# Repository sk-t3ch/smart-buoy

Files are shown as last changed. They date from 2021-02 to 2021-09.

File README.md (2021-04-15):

# [T3chFlicks](https://t3chflicks.org): Smart Buoy



> A complete ocean characteristic measuring and analytics system.
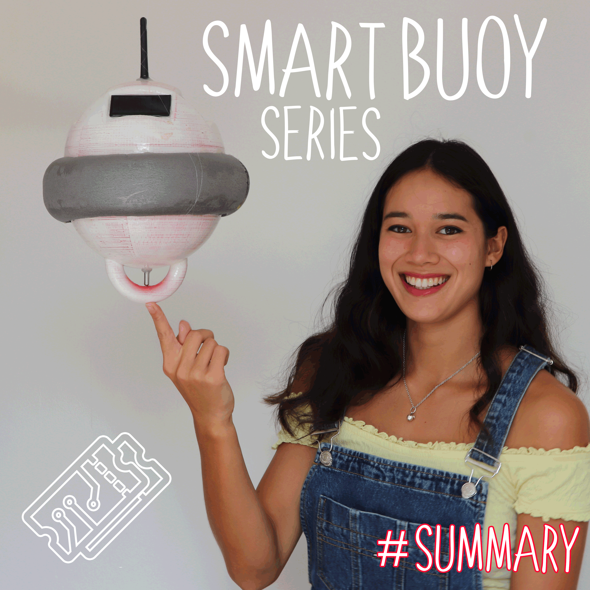
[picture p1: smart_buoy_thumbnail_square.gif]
gif_of_buoy


🎖️ Featured by [Raspberry Pi Blogs](https://www.raspberrypi.org/blog/good-buoy-the-raspberry-pi-smart-buoy/)

🎖️ Featured by [Hackaday](https://hackaday.com/2019/09/11/smart-buoy-rides-the-citizen-science-wave/)

🎖️ Featured by [Adafruit Blogs](https://blog.adafruit.com/2019/07/19/this-smart-buoy-measures-wave-height-period-power-and-more-piday-raspberrypi-raspberry_pi/)

🎖️ Featured by [Arduino](https://www.facebook.com/official.arduino/posts/3480468415312786)

🎖️ Featured by [Instructables](https://www.instructables.com/Smart-Buoy/)

🎖️ Second place [Instructables Sensor Contest](https://www.instructables.com/contest/sensors2019/)

---

## `tutorials/`
### Summary






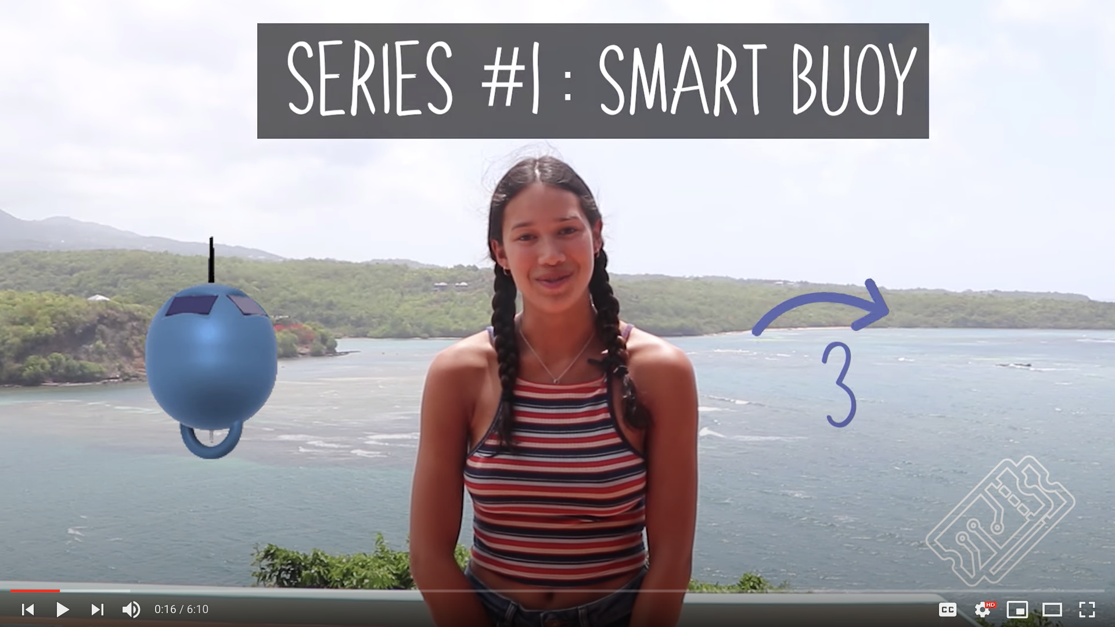
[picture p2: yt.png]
Everything Is AWESOME (https://www.youtube.com/watch?v=aLX4btGs_x8 "Youtube Video")
 

### 1. Wave and Temperature Measurements






### 2. GPS, Radio, and SD card






### 3. Scheduling Power






### 4. Waterproofing, Dashboards and Deploy






---

## `src/` - contains the source code for the whole project
* `buoy/` contains the code which runs on an Arduino inside the Buoy, as well as the build files (3d model, schematic etc).

* `baseStation/` contains the code for the server, database, and dashboard.
for the dashboard which is a VueJS application

---

## 💡 Product Showcase
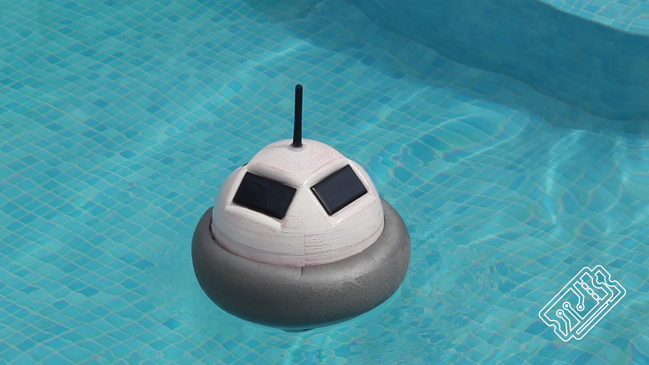
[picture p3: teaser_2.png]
Product
> 
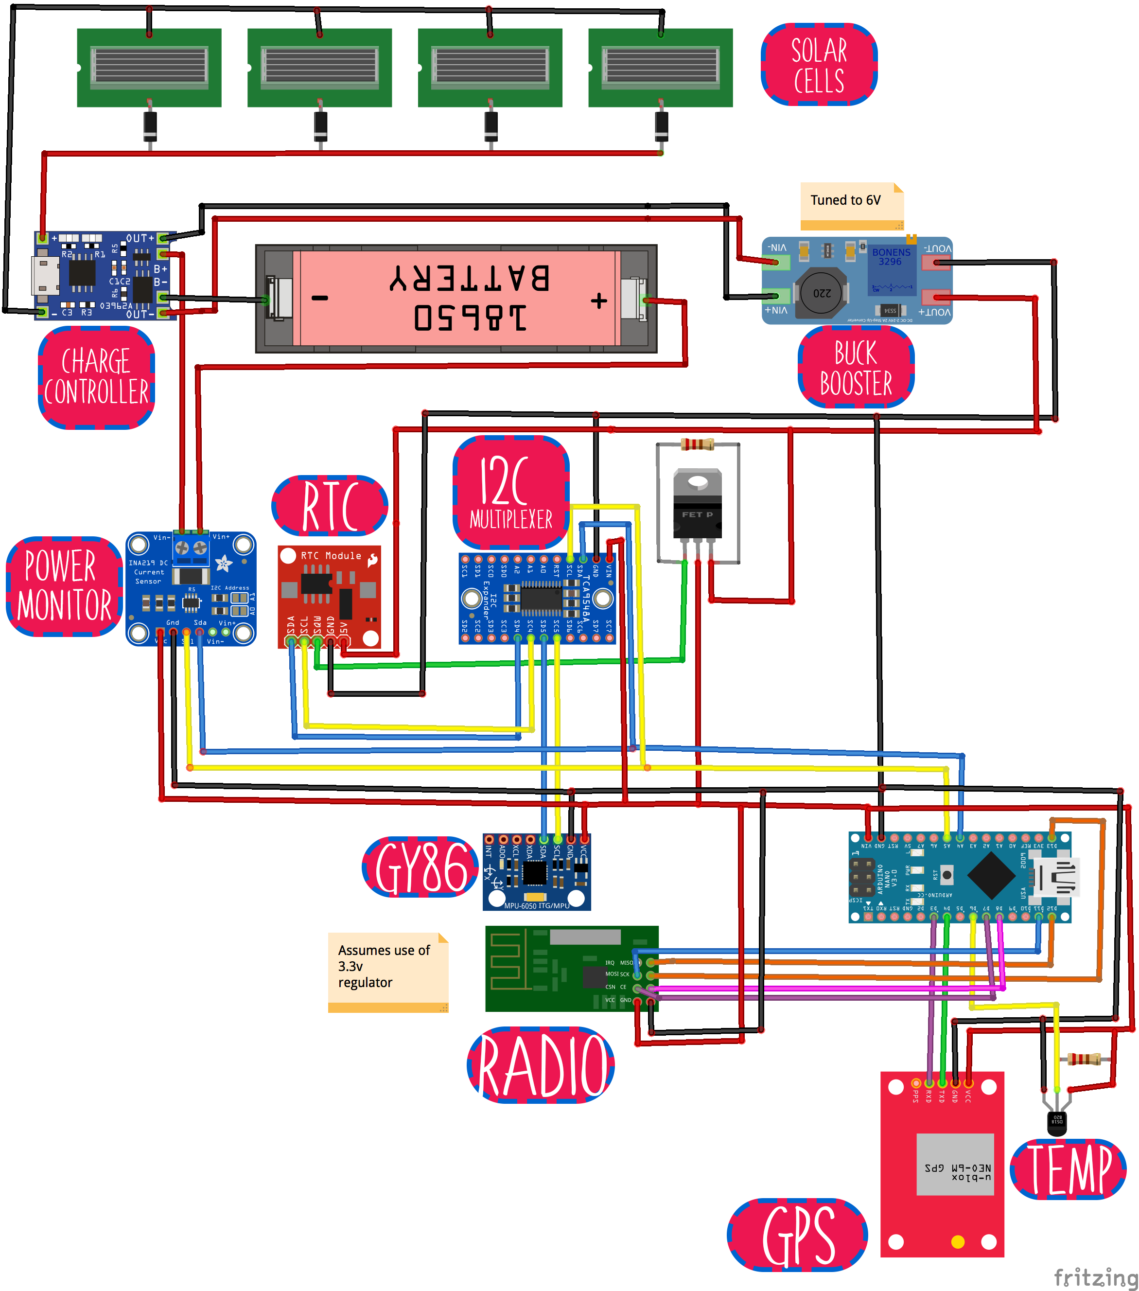
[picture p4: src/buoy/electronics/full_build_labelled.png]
Buoy Electronics
> 
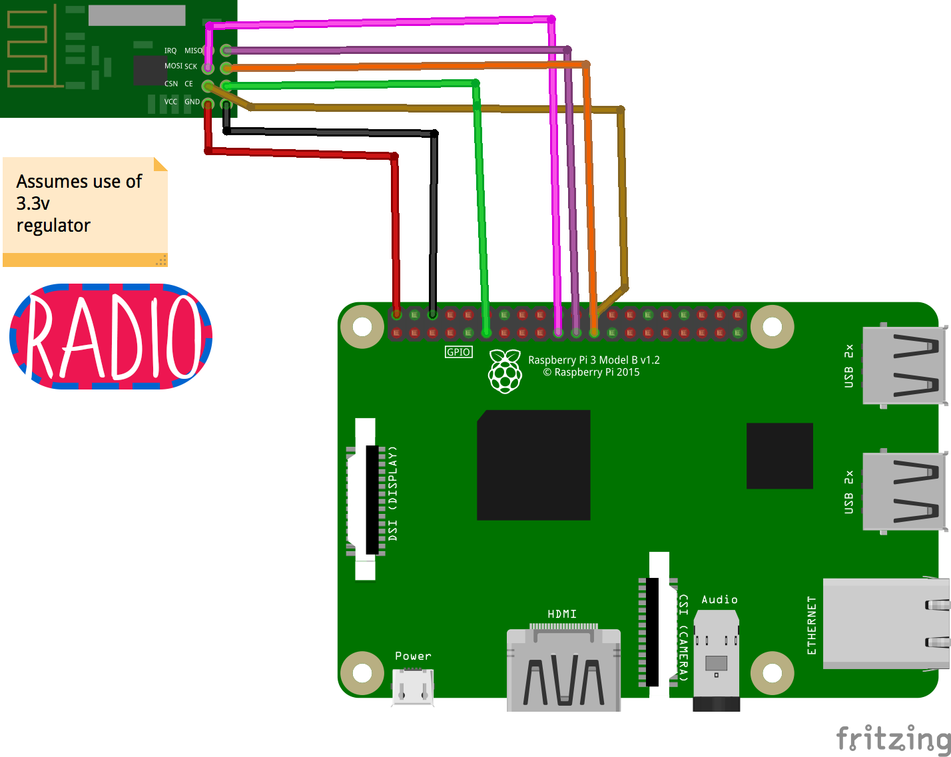
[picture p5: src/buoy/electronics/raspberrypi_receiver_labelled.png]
Buoy Electronics
> 
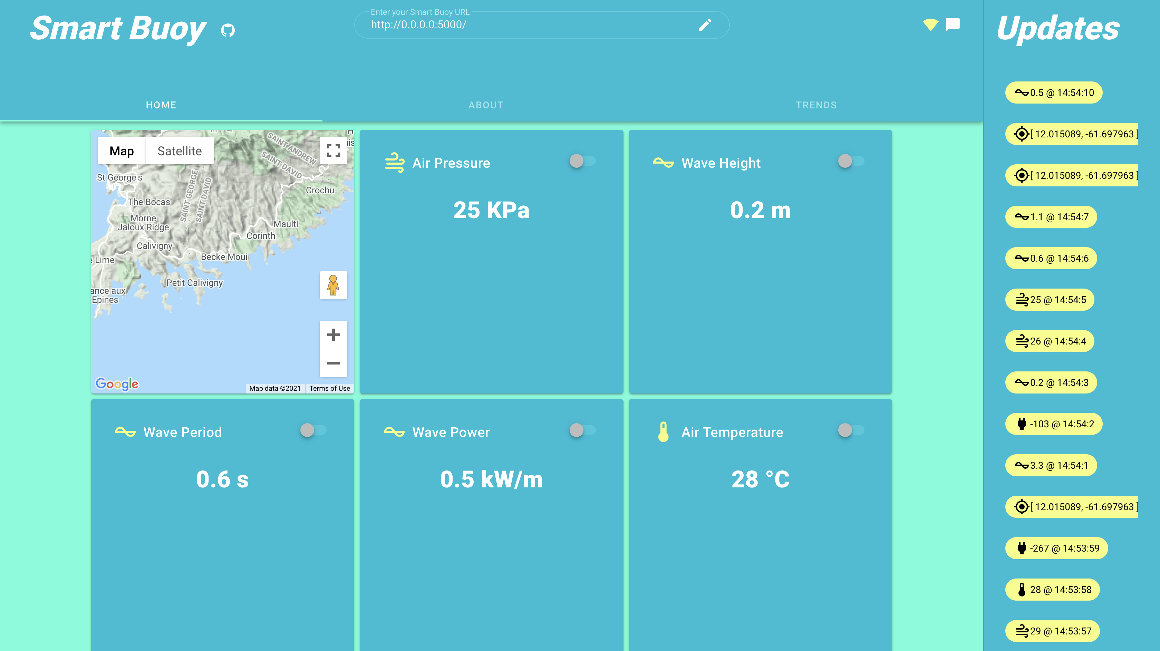
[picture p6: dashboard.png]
Buoy Dashboard Home
> 
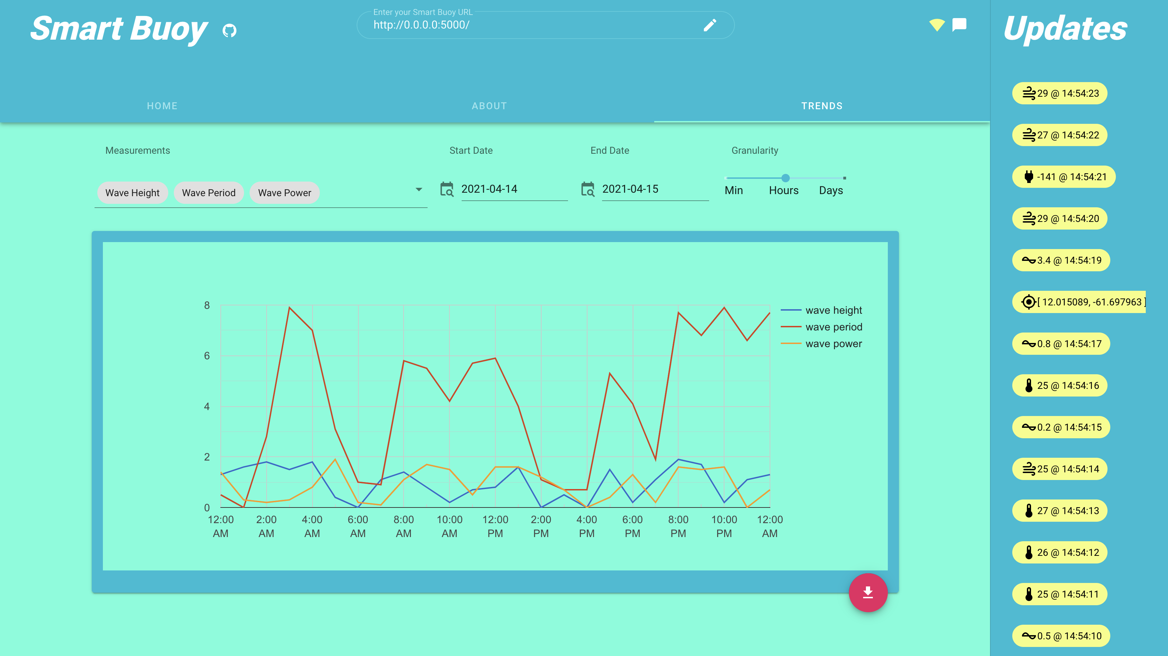
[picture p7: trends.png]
Buoy Dashboard Trends
> 
* Environment
  * Wave measurements
    * Size
    * Period
    * Power
    * Direction
    * Water temperature
  * Air
    * Temperature
    * Humidity
    * Pressure
  * Position (GPS)
* Power
  * Solar powered
  * Scheduled time for power based on battery voltage
* Radio Communication (Range 1KM)
* Interactive dashboard 
  * Realtime view
  * Graph historical measurements

---

This project was created by [T3chFlicks](https://t3chflicks.org) - A tech focused education and services company.

---

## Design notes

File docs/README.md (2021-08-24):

---
description: A complete ocean characteristic measuring and analytics system.
---

# Introduction

We all love the seaside. As a collective, we flock to it for holidays, to enjoy water sports or to make our livelihood. But the coast is a dynamic area at the mercy of waves. Rising sea levels nibble at beaches and powerful extreme events like hurricanes completely decimate them. To understand how to save them, we need to understand the forces driving their change.

Research is expensive, but if you could create cheap, effective instruments, you would be able to generate more data – ultimately improving understanding. This was the thinking behind our Smart Buoy project. In this summary, we give you a quick run down of our project and break it down into design, the make and data presentation. Oh buoy, you’re going to love this..!

gif\_of\_buoy

🎖️ Featured by [Raspberry Pi Blogs](https://www.raspberrypi.org/blog/good-buoy-the-raspberry-pi-smart-buoy/)

🎖️ Featured by [Hackaday](https://hackaday.com/2019/09/11/smart-buoy-rides-the-citizen-science-wave/)

🎖️ Featured by [Adafruit Blogs](https://blog.adafruit.com/2019/07/19/this-smart-buoy-measures-wave-height-period-power-and-more-piday-raspberrypi-raspberry_pi/)

🎖️ Featured by [Arduino](https://www.facebook.com/official.arduino/posts/3480468415312786)

🎖️ Featured by [Instructables](https://www.instructables.com/Smart-Buoy/)

🎖️ Second place [Instructables Sensor Contest](https://www.instructables.com/contest/sensors2019/)

[https://whimsical.com/smart-buoy-2x7PNzVxmZx7oKikP9o2LP](https://whimsical.com/smart-buoy-2x7PNzVxmZx7oKikP9o2LP)

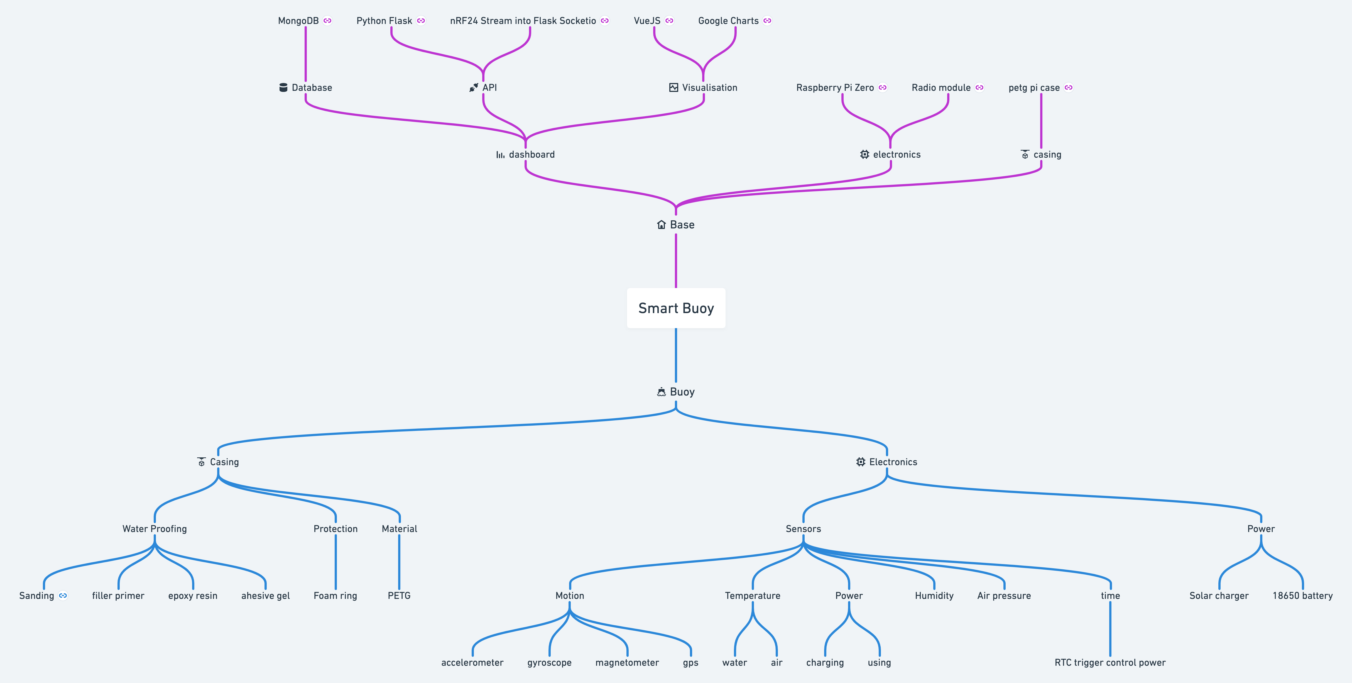
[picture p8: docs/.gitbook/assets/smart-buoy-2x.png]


## Dashboard

{% hint style="info" %}
Get a peak at the dashboard Generic badge (https://smart-buoy.t3chflicks.org/) 👈
{% endhint %}



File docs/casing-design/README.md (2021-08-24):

# Casing/Design

## Buoy two halves

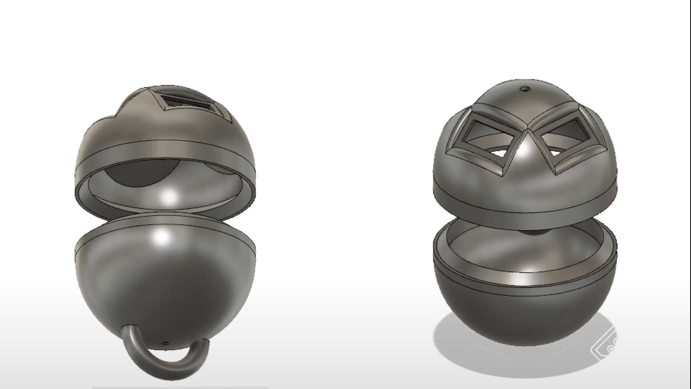
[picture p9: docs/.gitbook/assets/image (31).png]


{% embed url="https://github.com/sk-t3ch/smart-buoy/blob/master/src/buoy/3d/top.stl" %}

## Case for base station

Raspberry Pi Base Station can use any of a many number of open source cases on thingiverse

[https://www.thingiverse.com/thing:1595429](https://www.thingiverse.com/thing:1595429)

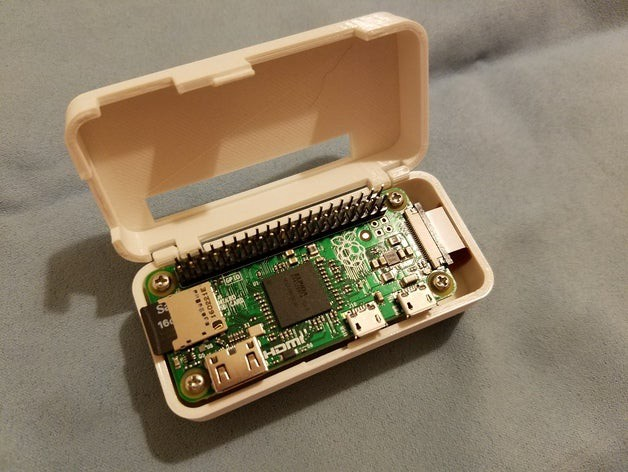
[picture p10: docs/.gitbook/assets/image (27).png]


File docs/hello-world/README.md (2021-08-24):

---
description: Measuremeeeee
---

# Hello World 🌎

## Earth

Earth is a spherical body composed of a gas and liquid on top of a solid crust and a middle liquid containing a solid core,

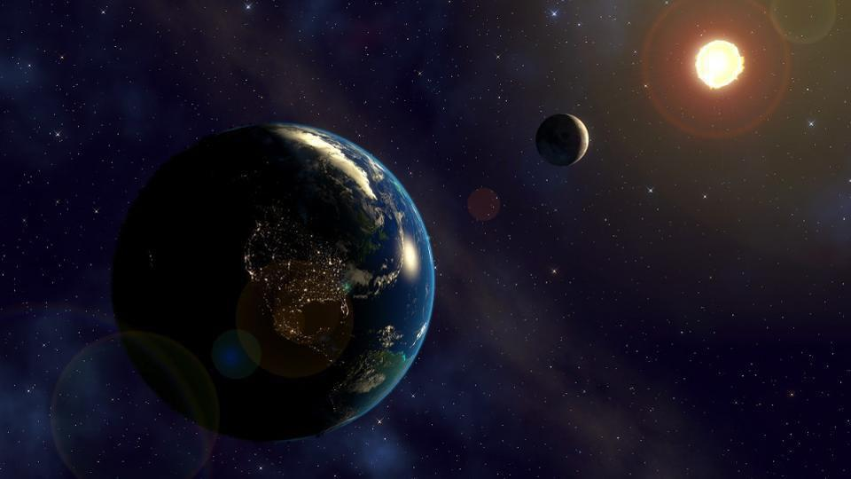
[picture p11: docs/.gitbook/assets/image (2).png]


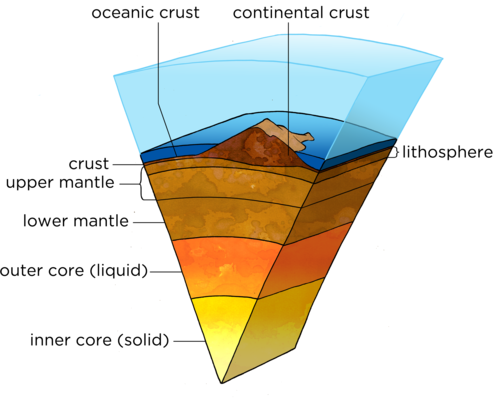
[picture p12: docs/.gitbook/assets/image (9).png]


## Moving Objects

Earth is located x from the sun. The Earth orbits the Sun at a speed of 365x24 h

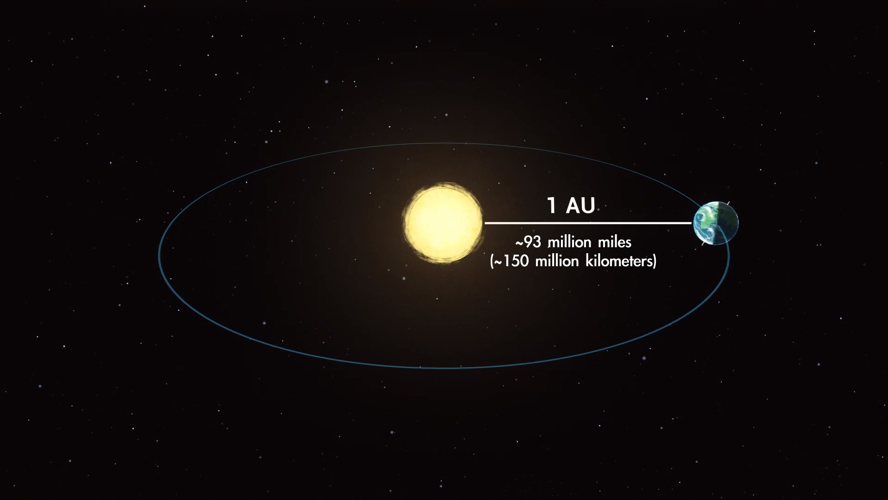
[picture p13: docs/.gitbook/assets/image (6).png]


Earth spins on an axis at a speed of 24hours that varies at a level of and a 

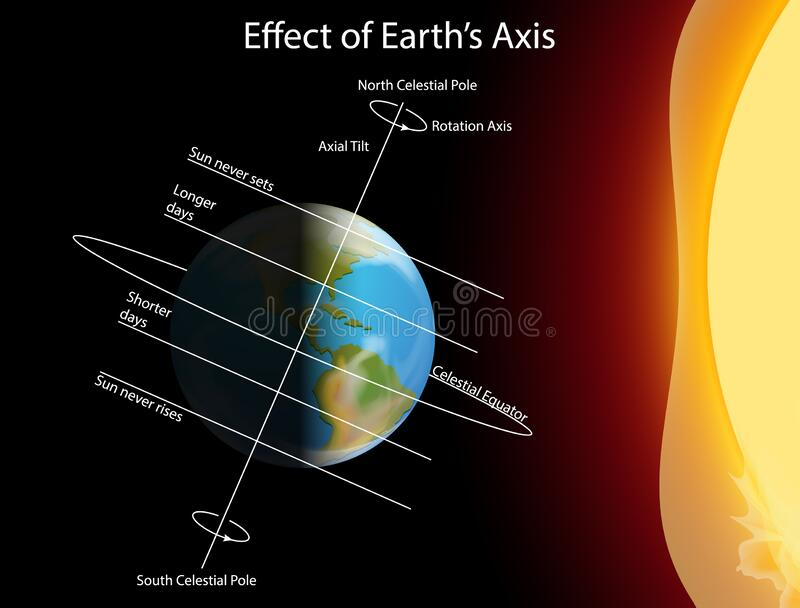
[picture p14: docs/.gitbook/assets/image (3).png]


The Sun provides Earth with energy which drives dynamism 

EM forces + EM waves

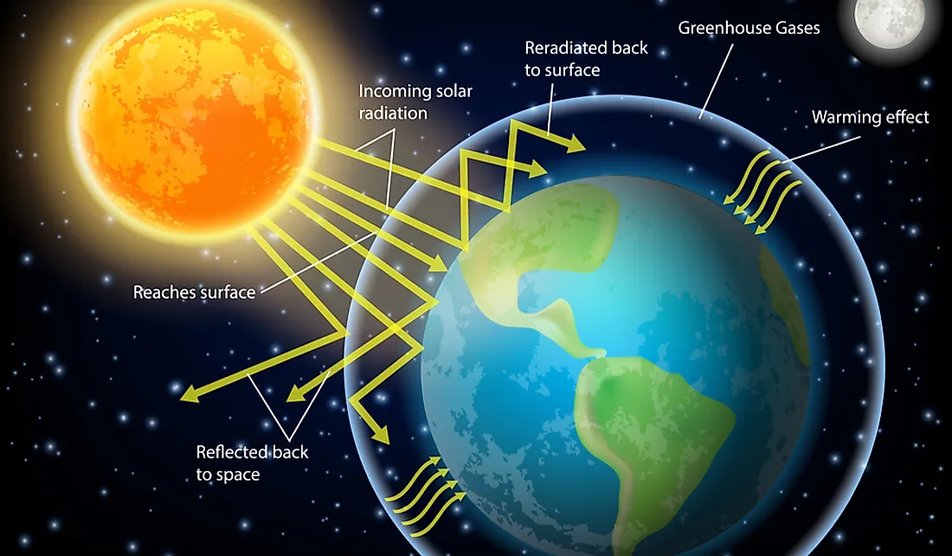
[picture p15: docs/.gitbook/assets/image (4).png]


Earth varies its axis on the orbit with the sun with a period of 90 days \(hint: seasons\)

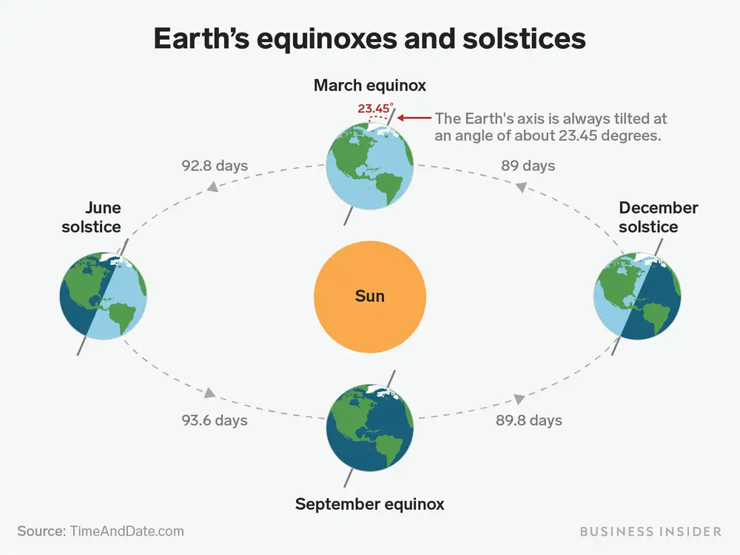
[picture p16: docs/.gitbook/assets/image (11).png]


Earth tilt

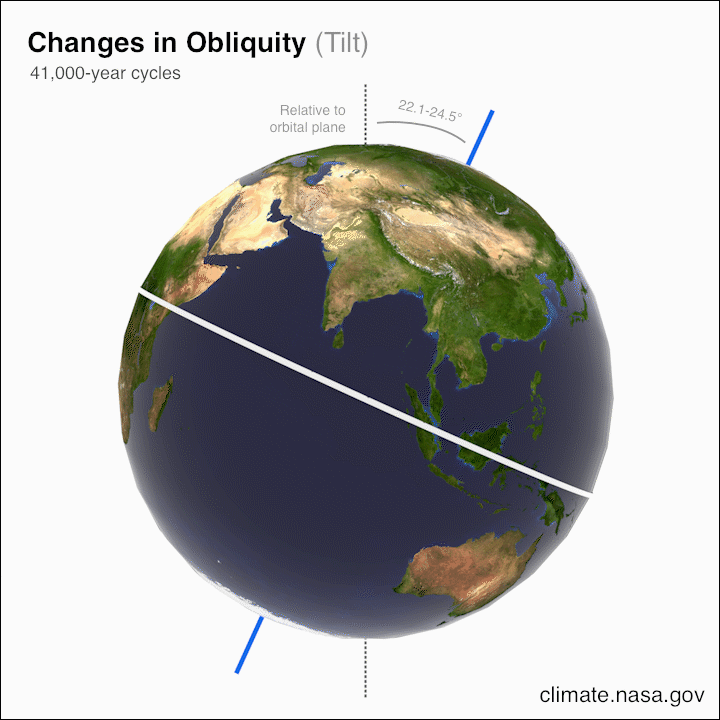
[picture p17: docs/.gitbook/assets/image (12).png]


## Magnetism

Earth is composed of mostly metals and other materials

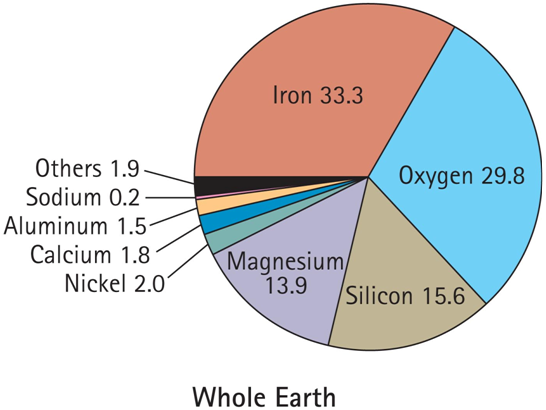
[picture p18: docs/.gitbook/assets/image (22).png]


specific property known as magnetism which they attract each other through the electromotive force this interaction gives rise to a global magnetic field. 

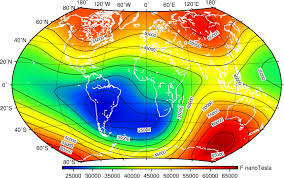
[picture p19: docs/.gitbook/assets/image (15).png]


## Gravitation

The mass of different materials also forms a global gravitational field which operates at a level of

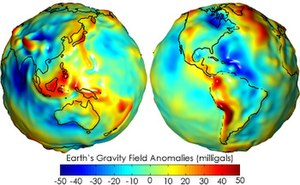
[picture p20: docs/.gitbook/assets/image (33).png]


The moon is a body composed of x which orbits Earth with a period of 28 days and a variation which gives rise to effects 

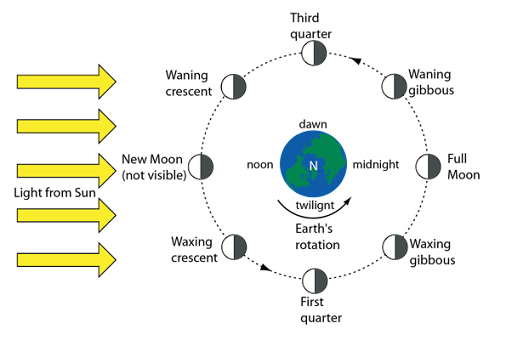
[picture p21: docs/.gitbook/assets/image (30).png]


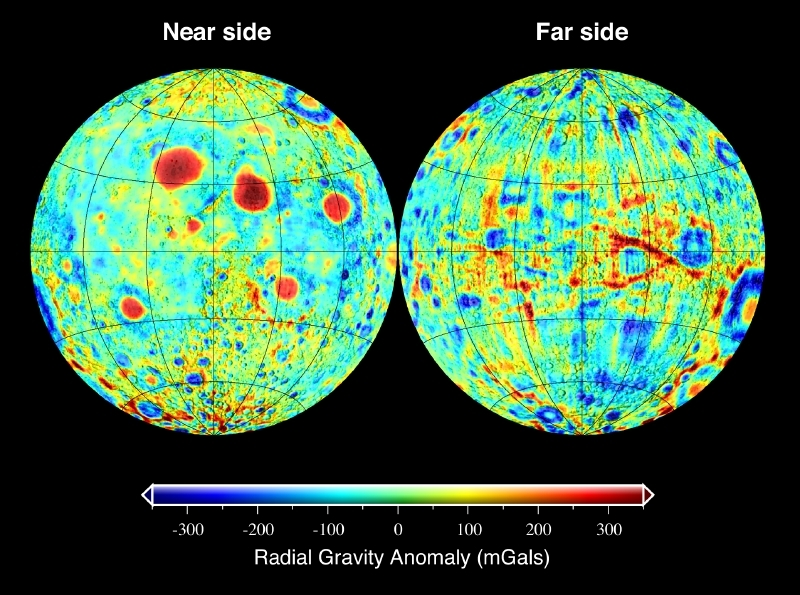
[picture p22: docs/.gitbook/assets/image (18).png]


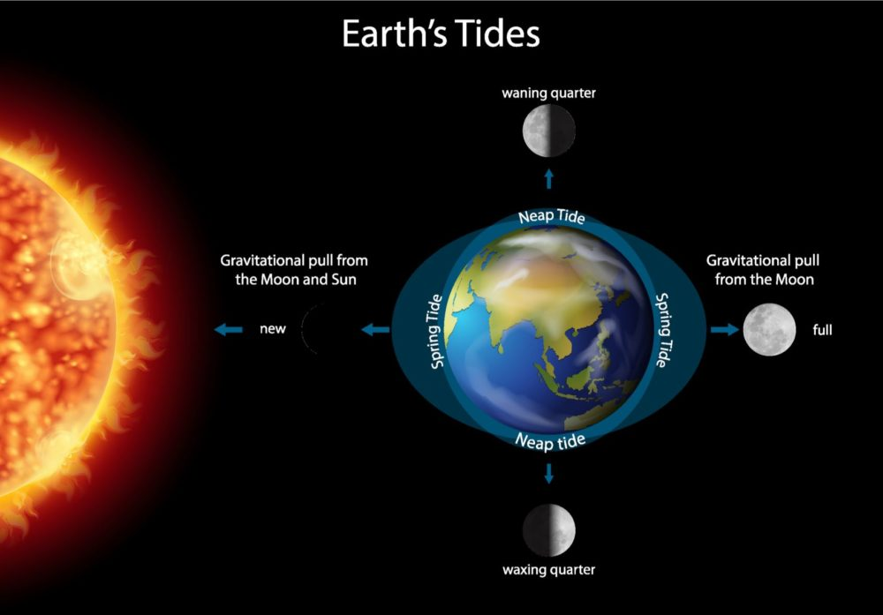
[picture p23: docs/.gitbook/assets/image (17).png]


The Earth has many interacting phenomena

About 70% of the Earth's surface is covered in water. 

The atmosphere is mostly made of water. 

But the 

## Water?

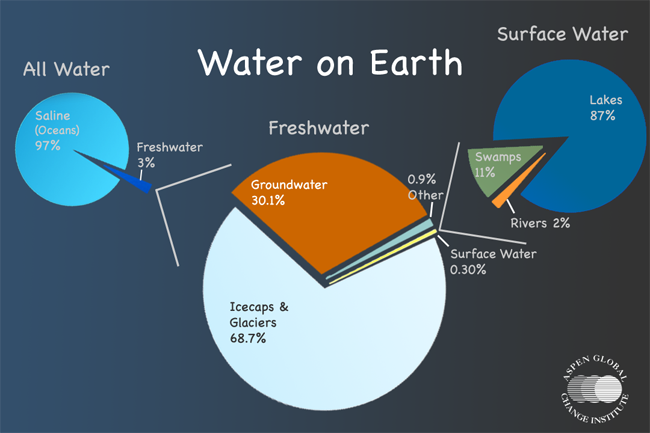
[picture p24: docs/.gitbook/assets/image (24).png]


x billion years ago Earth was formed

x billion years ago we expect Earth the be a totally different hostile environment

x billion years ago life began as we know it

> how did life use water?

x billion years ago fish left the sea to become land faring animals

x million years ago the first humanoid 

x thousand years ago the first modern anatomically humans

> now what do we use water for

Links Used:

* [https://en.wikipedia.org/wiki/Water\_distribution\_on\_Earth](https://en.wikipedia.org/wiki/Water_distribution_on_Earth)

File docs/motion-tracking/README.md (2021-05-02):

# Motion Tracking

* sensors
* sensor fusion
* algorithms 
* hardware
* problems to overcome
* possibility of accuracy 
* [ ] gps
* [ ] lidar
* [ ] camera
* [ ] accelerometer 
* [ ] gyroscope

{% hint style="success" %}
_Things are hard_
{% endhint %}

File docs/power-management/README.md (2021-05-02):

# Power Management

* solar
* state of the art low power
* power requirements of different elements

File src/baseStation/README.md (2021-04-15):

## BaseStation

This folder contains the code for the running the server for the
Smart Buoy Dashboard.



This code should be run on a Raspberry Pi, which has Python3 and mongoDB installed.

It uses Flask as a web server and communicates with the radio module (NRF24) and a mongo database.
Flask-socketio is used for communication with the frontend via websockets.

dashboard

trends

If you want to play around with the dashboard without a Smart Buoy setup then just run `python mock_app.py`, and you should be able to see the data coming in.

Also for development purposes there is a `populate_db.py` script which does what is says on the tin.

If you just want to see the data coming from the Buoy to the Raspberry Pi via radio then you can use the `listen_to_radio.py` script.

---

### Get Running
1. Put a raspian image from [here](https://www.raspberrypi.org/downloads/) onto your pi sd card using [etcher](https://www.balena.io/etcher/).
1. Plug in the *nRF24L01* before turning on as in the diagram in the electronics folder.
1. SSH into your pi (for the rest of the instructions stay in a terminal) and set up as usual [tutorial](https://www.youtube.com/watch?v=wvxCNQ5AYPg).
1. Install python3 - [tutorial](https://installvirtual.com/install-python-3-7-on-raspberry-pi/).
1. Install mongoDB - [tutorial](https://andyfelong.com/2019/01/mongodb-3-2-64-bit-running-on-raspberry-pi-3-with-caveats/). Create a DB in mongo called 'buoyDB' and a collection called 'buoyMeasurements'.
    1. `sudo apt-get install mongodb`
    1. `sudo service mongodb start`
    1. `mongo`
    1. `use buoyDB`
    1. `db.createCollection('buoyMeasurements')`
1. Install python dependencies `pip install -r requirements.txt`
7. Update the fields in `frontend/.env` to use your google maps api key (https://developers.google.com/maps/documentation/javascript/get-api-key) and your Raspberry Pis IP address.
1. Build the frontend:
    1. `cd frontend`
    1. `npm i`
    1. `npm run build`

1. Start the server `python app.py`
1. Go to your browser on your pi's IP address or to the  and enter your IP address to connect the dashboard to the Pi and measurements should begin to stream in.

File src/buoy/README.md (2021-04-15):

### Buoy Stuff

`smart_buoy/` contains the Arduino code.

`3d/` contains the STL files for 3D printing the buoy shell.

`electronics/` contains the schematics for the electronics of both buoy and base station.

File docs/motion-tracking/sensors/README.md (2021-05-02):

# Sensors

* [ ] gps
* [ ] lidar
* [ ] camera
* [ ] accelerometer 
* [ ] gyroscope

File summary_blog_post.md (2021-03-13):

# Smart Buoy — Summary

We all love the seaside. As a collective, we flock to it for holidays, to enjoy water sports or to make our livelihood. But the coast is a dynamic area at the mercy of waves. Rising sea levels nibble at beaches and powerful extreme events like hurricanes completely decimate them. To understand how to save them, we need to understand the forces driving their change.

Research is expensive, but if you could create cheap, effective instruments, you would be able to generate more data – ultimately improving understanding. This was the thinking behind our Smart Buoy project. In this summary, we give you a quick run down of our project and break it down into design, the make and data presentation. Oh buoy, you’re going to love this..!



## Supplies:

For the complete Smart Buoy build, you need a LOT of stuff. We will have the breakdown of specific materials required for each stage of the build in the relevant tutorial, but here’s the complete list:

* Arduino Nano — [Amazon](https://amzn.to/2jJN7xR)

* Raspberry Pi Zero — [Amazon](https://amzn.to/2jHpV3D)

* Battery (18650) — [Amazon](https://amzn.to/2ld11cp)

* Solar panels — [Amazon](https://amzn.to/2ld2vmZ)

* Blocking Diodes — [Amazon](https://amzn.to/2ld2X4F)

* Charge controller — [Amazon](https://amzn.to/2jJhRz0)

* Buck booster — [Amazon](https://amzn.to/2jFnCxX)

* GPS module — [Amazon](https://amzn.to/2jHgwJ2)

* GY-86 (accelerometer, gyroscope, barometer, compass) — [Amazon](https://amzn.to/2ld5bB3)

* Water Temperature sensor — [Amazon](https://amzn.to/2lbTASO)

* Power monitor module — [Amazon](https://amzn.to/2lbU5MG)

* Real time clock module — [Amazon](https://amzn.to/2ld6yjb)

* Radio modules — [Amazon](https://amzn.to/2l6Fq5t)

* i²c multiplexer module — [Amazon](https://amzn.to/2jJnP2S)

* 3D printer — [Amazon](https://amzn.to/2ld7xQp)

* PETG filament — [Amazon](https://amzn.to/30yw95r)

* Epoxy — [Amazon](https://amzn.to/2lbVRNQ)

* Primer spray paint — [Amazon](https://amzn.to/2ld55cE)

* Rope — [Amazon](https://amzn.to/2jHkjWM)

* Floats — [Amazon](https://amzn.to/2lfTZ6R)

* Glue — [Amazon](https://amzn.to/2jFpeaZ)
> # [🔗 Get The Smart Buoy Code On Github 📔](https://github.com/sk-t3ch/smart-buoy)

## What Does It Do?

The sensors on board the Smart Buoy enable it to measure: wave height, wave period, wave power, water temperature, air temperature, air pressure, voltage, current usage and GPS location.

In an ideal world, it would also have measured wave direction. Based on the measurements the Buoy did take, we were quite close to finding a solution which would enable us to calculate wave direction. However, it turned out to be pretty complicated and it’s a massive problem in the actual research community. If there’s anyone out there who can help us out and suggest an effective way to get wave direction measurements, please let us know — we’d love to understand how we could get it to work!

All the data the Buoy collects is sent via radio to a base station, which is a Raspberry Pi. We made a dashboard to display them using Vue JS.

## Build 🛠️

### Buoy Casing

Sand with gradually softer levels of grit*

Sand with gradually softer levels of grit*

This Buoy was probably the most difficult thing we’ve printed so far. There were just so many things to take into consideration as it was going to be in the sea, exposed to the elements and a lot of sun. We will talk more about that later in the Smart Buoy series.

In brief: we printed a near hollow sphere in two halves. The top half has slots for the solar panels and a hole for a radio aerial to go through. The bottom half has a hole for a temperature sensor to go through and a handle for a rope to be tied to.

Spray-painting the PETG Buoy print with plastic primer filler*

Spray-painting the PETG Buoy print with plastic primer filler*

After printing the Buoy using PETG filament, we sanded it, spray painted it with some filler primer, and then put on a couple of layers of epoxy.

Painting epoxy on the Buoy*

Painting epoxy on the Buoy*

Epoxy covered top half of Buoy with solar panels*

Epoxy covered top half of Buoy with solar panels*

Once the prep of the shell was complete, we put all the electronics inside and then sealed the water temperature sensor, radio aerial and solar panels using a glue gun. Finally, we sealed the two halves with StixAll glue/adhesive (super aeroplane glue).



And then we hoped it was waterproof…



### Buoy Electronics

The Buoy has lots of sensors on board and we go into detail about these in the relevant tutorial. As this is a summary, we’ll try to keep this informative, but brief!

The Buoy is powered by an 18650 battery, which is charged by four, 5V solar panels. Only the real time clock is constantly powered, however. The Buoy uses the real time clock’s output pin to control a transistor allowing power to enter the rest of the system. When the system is turned on, it starts by getting measurements from the sensors — including a voltage value from the power monitor module. The value given by the power monitor module determines how long the system sleeps for before taking the next set of readings. An alarm is set for this time, then the system turns itself off!







The system itself is a lot of sensors and a radio module connected to an Arduino. The GY-86 module, RealTimeClock (RTC), Power Monitor module, and I2C multiplexer all communicate with the Arduino using I2C. We needed the I2C multiplexer is required because the GY-86 and the RTC module we used both have the same address. The multiplexer module allows you to communicate with no extra hassle, although it might be a bit overkill.



The radio module communicates via SPI.

Originally, we had an SD card module as well, but it caused so many headaches because of the size of the SD library that we decided to scrap it.



[Take a look at the code](https://github.com/sk-t3ch/smart-buoy). It’s likely that you have some questions — probably lingering doubts as well — and we’d be happy to hear them. The in-depth tutorials include code explanations, so hopefully they will make it a bit clearer!

We tried to logically separate the code files and use a main file to include them, which seemed to work pretty well.



### Base Station Electronics

The base station is made using a Raspberry Pi Zero with a radio module attached. We got the casing from [https://www.thingiverse.com/thing:1595429](https://www.thingiverse.com/thing:1595429). You’re fab, thanks so much!



Once you have the code running on the Arduino, it’s quite simple to get the measurements on the Raspberry Pi by running the `listen_to_radio.py` code.

### Dashboard

To show you how we made the entire dash would be a bit of an Odyssey because it was a pretty long and complicated project. If anyone wants to know how we did it, do let us know — the T3ch Flicks resident web developer would be more than happy to do a tutorial on this!



Once you put these files onto a Raspberry Pi, you should be able to run the server and see the dashboard with the data coming in. For development reasons and to see what the dash would look like if it were supplied by good, regular data, we added a fake data generator into the server. Run that if you want to see what it looks like when you have more data. We’ll also explain this in some detail in a later tutorial.
> # [🔗 Get The Smart Buoy Code On Github 📔](https://github.com/sk-t3ch/smart-buoy)





## Version 2??

### Problems

This project is absolutely not perfect — we like to think of it more as a prototype/proof of concept. Although the prototype works on a fundamental level: it floats, takes measurements and it able to transmit them, there are lots of we’ve learned and would change for version two:

1. Our biggest issue was not being able to change the code for the Buoy after gluing it shut. This was really a bit of an oversight and could be solved very effectively with a USB port covered with a rubber seal. That, however, would have added a whole other layer of complexity to the 3D print waterproofing process!

1. The algorithms we used were far from perfect. Our methods for determining wave properties were pretty crude and we ended up spending a lot of our time reading up on math for combining the sensor data from the magnetometer, accelerometer, and gyroscope. If someone out there understands this and is willing to help, we think we could make these measurements much more accurate.

1. Some of the sensors acted a little bit weirdly. The water temperature sensor was the one which stood out as being particularly dodgy — almost 10 degrees out from the real temperature at times. The reason for this could have been it just being a bad sensor, or something was heating it up…

### Improvements

The Arduino was good, but as mentioned before we had to scrap the SD card module (which was supposed to be the data backup if radio messages weren’t able to send) due to memory issues. We could change it to a more powerful microcontroller like an Arduino Mega or a Teensy or just use another Raspberry Pi zero. However, this would have increased cost and power consumption.

The radio module we used has a limited range of a [couple of kilometres with direct line of sight](https://www.youtube.com/watch?v=57pdX6b0sfw).

However, in a hypothetical world where we were able to put (very) many Buoys around the island, we could have formed a [mesh network like this](https://www.youtube.com/watch?v=xb7psLhKTMA). There are so many possibilities for long range transmission of data, including lora, grsm. If we were able to use one of these, maybe a mesh network around the island would be possible!

## Using Our Smart Buoy for Research

We built and launched the Buoy in Grenada, a small island in the south Caribbean. While we were out there, we had a chat with the Grenadian government, who said that a Smart Buoy like the one we created would be helpful in providing quantitative measurements of ocean characteristics. Automated measurements would cut out some human effort and human error and provide helpful context for understanding changing coasts. The government also suggested that taking wind measurements would also be a helpful feature for their purposes. No idea how we’re going to manage that one, so if anyone has any ideas…

An important caveat is that although it’s a really exciting time for coastal research, particularly involving tech, there’s a long way to go before it can be fully adopted.



## Thanks For Reading

Thanks for reading the Smart Buoy series summary blog post. If you haven’t already, please take a look at our [summary video on YouTube](https://www.youtube.com/watch?v=S-XMT6GDWk8).

[**Part 1**: Making wave and temperature measurements](https://link.medium.com/Y3knMlmmBeb)

[**Part 2**: GPS, Radio (NRF24) and SD Card Module](https://link.medium.com/Oev2Ia1lBeb)

[**Part 3**: Scheduling Power to the Buoy](https://link.medium.com/vte3uQdmBeb)

[**Part 4**: Waterproofing, Dashboards and Deploy!](https://link.medium.com/qEv9AIhmBeb)

I hope you have enjoyed this article. If you like the style, check out [T3chFlicks.org](https://t3chflicks.org/) for more tech focused educational content ([YouTube](https://www.youtube.com/channel/UC0eSD-tdiJMI5GQTkMmZ-6w), [Instagram](https://www.instagram.com/t3chflicks/), [Facebook](https://www.facebook.com/t3chflicks), [Twitter](https://twitter.com/t3chflicks)).

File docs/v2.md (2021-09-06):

# V2

Requirements:

* open source
* 3d printed
* under $200
* PCB easy accessible components
* modular and expansive
* raspberry pi powered
* community driven

Things it can do:

* measure air
* measure ocean waves
* solar powered
* network with other buoys
* cool dash
  * realtime dash

similar products - [https://www.sofarocean.com/products/spotter](https://www.sofarocean.com/products/spotter)

**Example**

* _navio2_ 
  * accelerometer gyroscope
  * double gps
  * radio telemetry
  * FPV camera
  * run custom scripts
* loRA radio module

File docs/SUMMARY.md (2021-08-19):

# Table of contents

* [Introduction](README.md)
* [Hello World 🌎](hello-world/README.md)
  * [Atmosphere](hello-world/atmosphere.md)
  * [Waves](hello-world/waves/README.md)
    * [Period](hello-world/waves/period.md)
    * [Height](hello-world/waves/height.md)
    * [Power/Energy](hello-world/waves/power-energy.md)
    * [Direction](hello-world/waves/direction.md)
  * [Useful Links](hello-world/useful-links.md)
* [Motion Tracking](motion-tracking/README.md)
  * [Useful Links](motion-tracking/useful-links.md)
  * [Sensors](motion-tracking/sensors/README.md)
    * [Compass/Magnetometer](motion-tracking/sensors/compass-magnetometer.md)
    * [Barometer](motion-tracking/sensors/barometer.md)
    * [GPS](motion-tracking/sensors/gps.md)
    * [Accelerometer](motion-tracking/sensors/accelerometer.md)
    * [Gyroscope](motion-tracking/sensors/gyroscope.md)
    * [Camera](motion-tracking/sensors/camera.md)
  * [Sensor Fusion](motion-tracking/sensor-fusion.md)
* [Power Management](power-management/README.md)
  * [Battery](power-management/battery.md)
  * [Charging](power-management/charging.md)
  * [Solar](power-management/solar.md)
  * [Low power](power-management/low-power.md)
* [Networking](networking/README.md)
  * [Radio](networking/radio.md)
  * [LoRa](networking/lora.md)
  * [WiFi](networking/wifi.md)
* [Casing/Design](casing-design/README.md)
  * [Design](casing-design/design.md)
  * [Printing](casing-design/printing.md)
* [Base Station](base-station/README.md)
  * [Server](base-station/server.md)
  * [Storage](base-station/storage.md)
  * [Dashboard](base-station/dashboard.md)
* [Other Measurements](other-measurements/README.md)
  * [Air Temperature](other-measurements/air-temperature.md)
  * [Water Temperature](other-measurements/water-temperature.md)
  * [Humidity](other-measurements/humidity.md)
  * [pH](other-measurements/ph.md)
  * [Salinity](other-measurements/salinity.md)
  * [Oxygen](other-measurements/oxygen.md)
* [Research](research/README.md)
  * [Existing Projects](research/existing-projects.md)
* [V1](v1/README.md)
  * [Buoy](v1/buoy.md)
  * [Base Station](v1/base-station.md)
  * [Blog Posts](v1/original-blogs/README.md)
    * [Summary](v1/original-blogs/summary.md)
    * [Making Wave and Temperature Measurements 🌊🌡️](v1/original-blogs/wave-and-temperature-measurements.md)
    * [GPS, Radio \(NRF24\) and a SD Card Module 📍📡💾](v1/original-blogs/gps-radio-nrf24-and-a-sd-card-module.md)
    * [Scheduling Power to the System🔋⌛](v1/original-blogs/scheduling-power-to-the-system.md)
    * [Waterproofing, Dashboards and Deploy 🚱📊](v1/original-blogs/waterproofing-dashboards-and-deploy.md)
  * [Review](v1/review.md)
* [V2](v2.md)
* [Buy us a coffee ☕](buy-us-a-coffee.md)

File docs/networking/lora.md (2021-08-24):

# LoRa

### Example Sensor

* LoRa radio module [https://www.amazon.co.uk/dp/B07BPQXXQ5](https://www.amazon.co.uk/dp/B07BPQXXQ5)

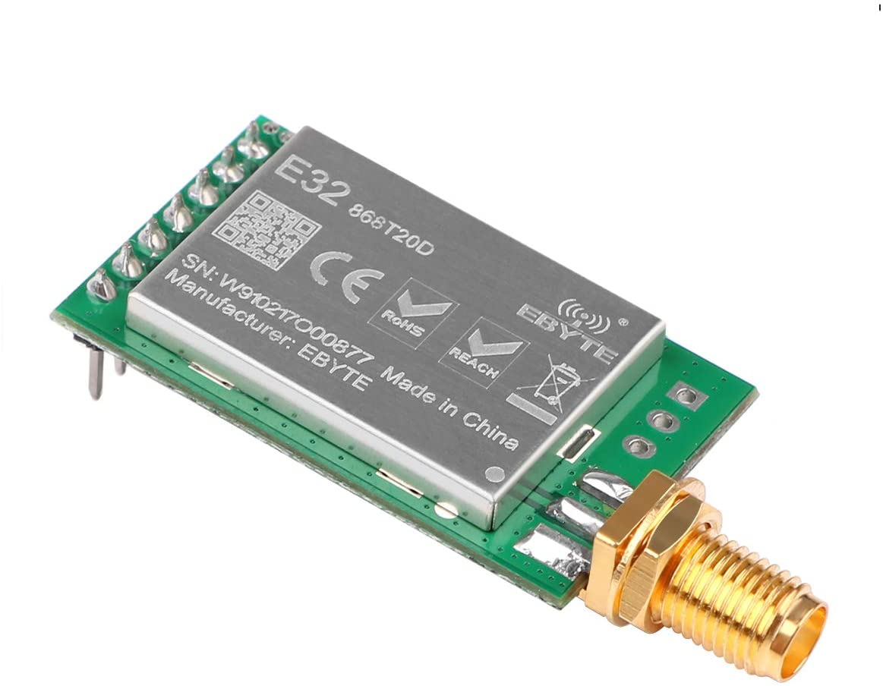
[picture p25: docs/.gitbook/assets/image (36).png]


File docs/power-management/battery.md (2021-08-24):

# Battery

Example

* 18650 2500mAh [https://www.fogstar.co.uk/collections/batteries/products/samsung-25r-br-2500mah-20a](https://www.fogstar.co.uk/collections/batteries/products/samsung-25r-br-2500mah-20a) 

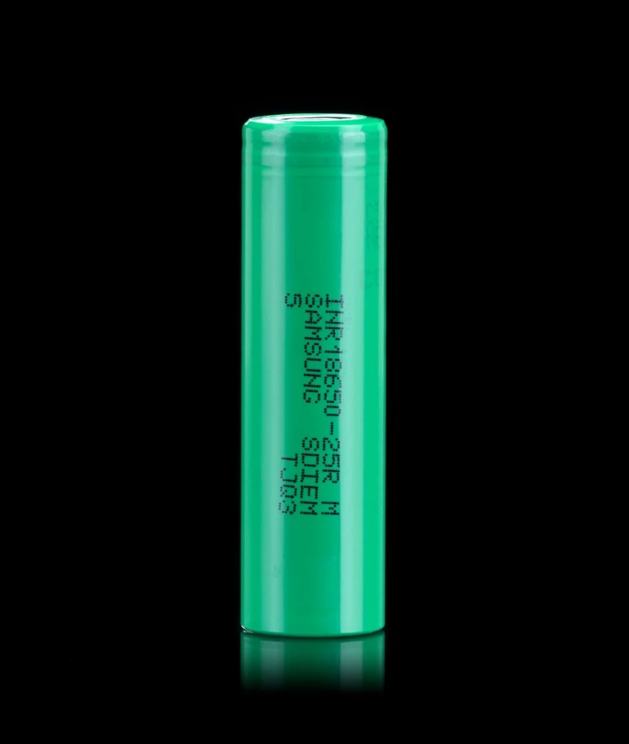
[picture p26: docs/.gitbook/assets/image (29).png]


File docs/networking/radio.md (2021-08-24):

# Radio

### Example Sensor

* NRF24L01 Radio Sensor [https://www.amazon.co.uk/WayinTop-NRF24L01-Transceiver-Regulator-Compatible/dp/B07P95X6HM](https://www.amazon.co.uk/WayinTop-NRF24L01-Transceiver-Regulator-Compatible/dp/B07P95X6HM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)

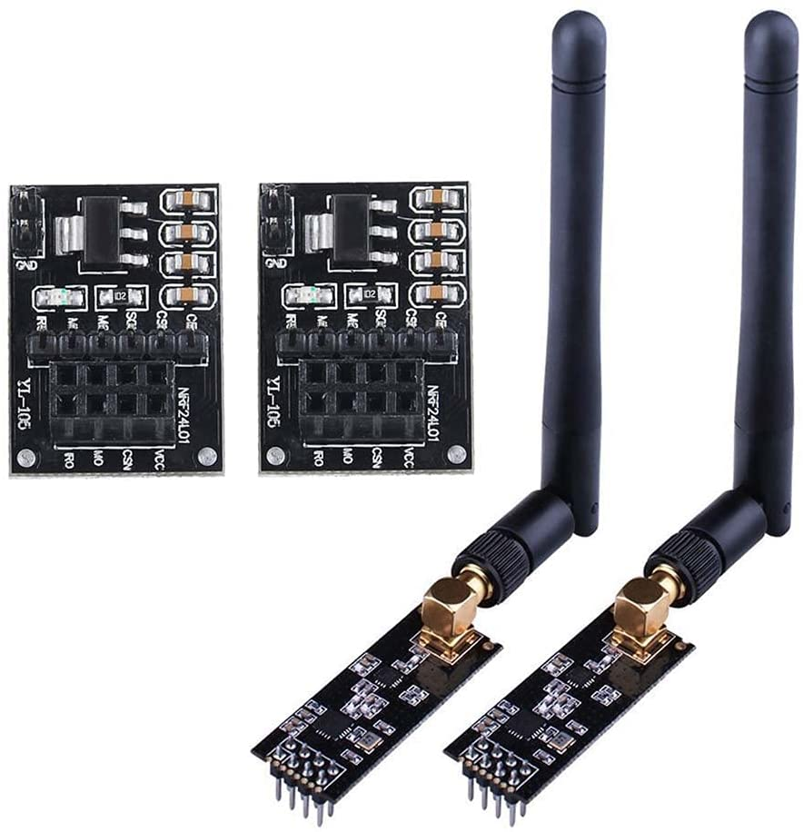
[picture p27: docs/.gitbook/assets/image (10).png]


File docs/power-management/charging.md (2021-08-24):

# Charging

### 

### Example Sensor

* 18650 charger [https://www.amazon.co.uk/TP4056-Lithium-Charging-Protection-Function/dp/B07BSVS842](https://www.amazon.co.uk/TP4056-Lithium-Charging-Protection-Function/dp/B07BSVS842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)

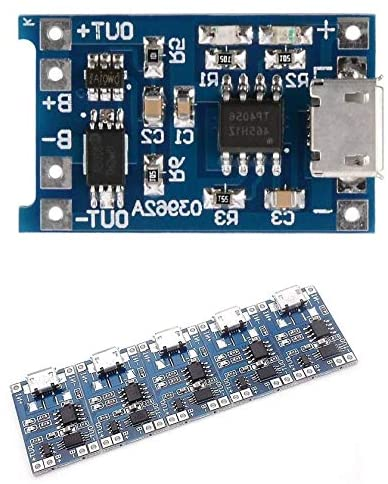
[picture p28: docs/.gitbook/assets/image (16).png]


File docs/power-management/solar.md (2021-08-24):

# Solar

### Example Sensor

* 4 X 0.6W 5V Solar Cells [https://www.amazon.co.uk/Keenso-Polysilicon-Charging-Charger-Appliances/dp/B0814WF3HJ](https://www.amazon.co.uk/Keenso-Polysilicon-Charging-Charger-Appliances/dp/B0814WF3HJ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)

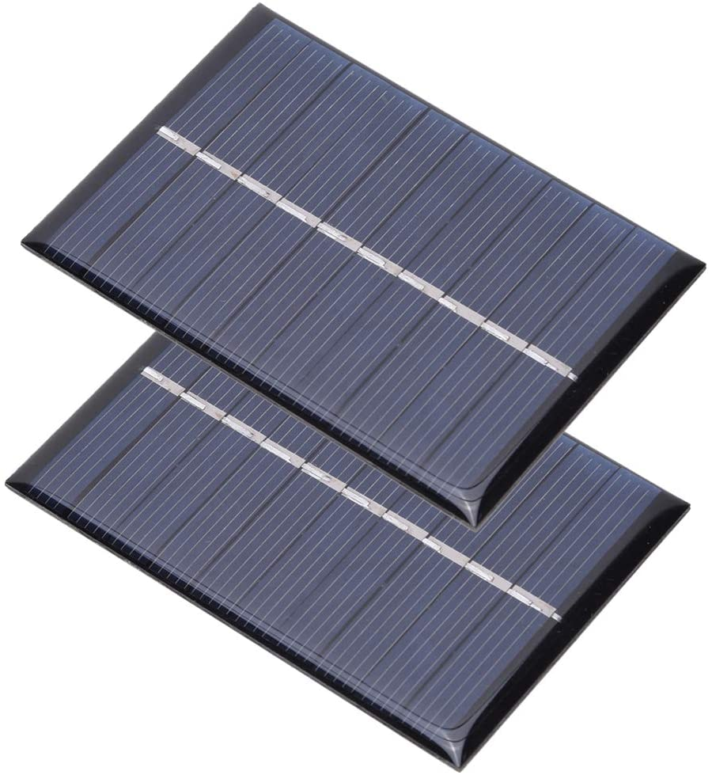
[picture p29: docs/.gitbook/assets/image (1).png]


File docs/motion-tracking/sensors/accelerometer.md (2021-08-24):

# Accelerometer

### Example Sensor

* MP-6050 has an accelerometer [https://www.amazon.co.uk/ALMOCN-MPU-6050-Gyroscope-Accelerometer-Converter/dp/B08ZN5964F/](https://www.amazon.co.uk/ALMOCN-MPU-6050-Gyroscope-Accelerometer-Converter/dp/B08ZN5964F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)

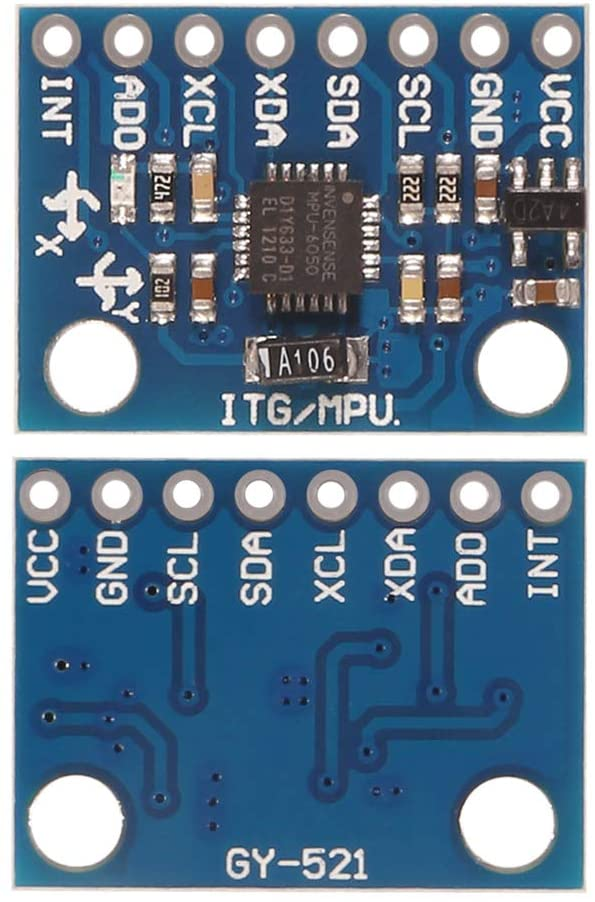
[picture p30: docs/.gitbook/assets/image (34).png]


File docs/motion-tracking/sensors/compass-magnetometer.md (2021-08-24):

# Compass/Magnetometer

### Example Sensor

* QMC5883L Magnetometer Sensor [https://www.amazon.co.uk/ALMOCN-QMC5883L-Compass-Magnetometer-Accurancy/dp/B091T9NL5B](https://www.amazon.co.uk/ALMOCN-QMC5883L-Compass-Magnetometer-Accurancy/dp/B091T9NL5B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)

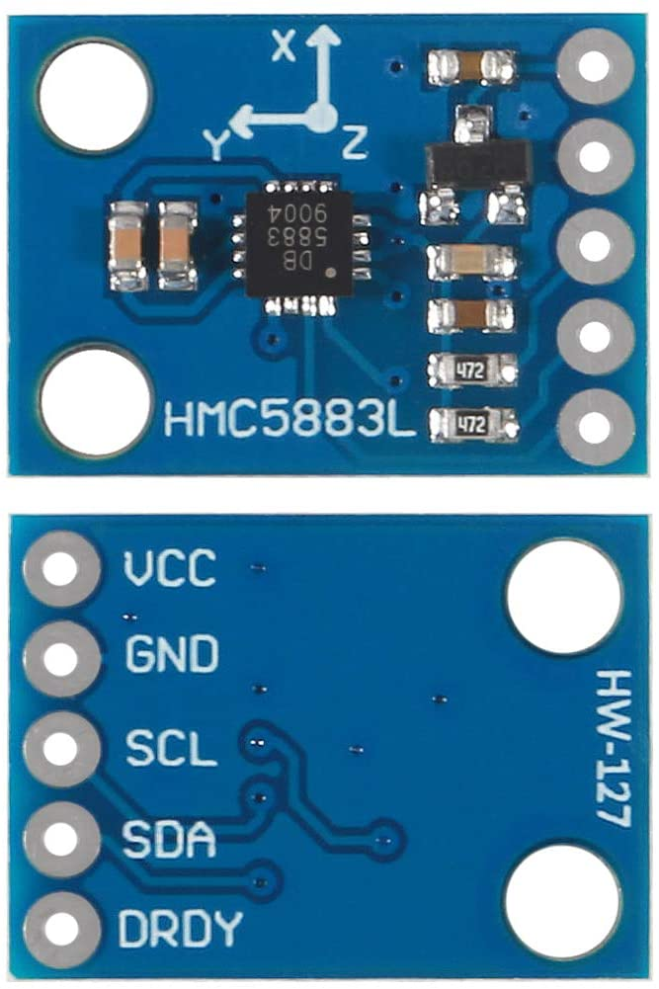
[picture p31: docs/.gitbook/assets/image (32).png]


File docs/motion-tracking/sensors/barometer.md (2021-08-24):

# Barometer

### Example Sensor 

BMP180 Barometric sensor [https://www.amazon.co.uk/AITRIP-Digital-Barometric-Pressure-Replace/dp/B08Y135YQJ](https://www.amazon.co.uk/AITRIP-Digital-Barometric-Pressure-Replace/dp/B08Y135YQJ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)



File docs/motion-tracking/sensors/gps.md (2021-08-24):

# GPS

### Example Sensor

* GPS sensor [https://www.amazon.co.uk/Receiver-Navigation-Raspberry-Betaflight-DIYmalls/dp/B082VBHQLZ](https://www.amazon.co.uk/Receiver-Navigation-Raspberry-Betaflight-DIYmalls/dp/B082VBHQLZ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)

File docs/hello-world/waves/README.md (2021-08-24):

# Waves

What are waves?

What systems exists?

What can we measure about these systems?

What will our measurements tell us about the systems?





## Energy

Wave energy is a good way to look at the system

spectrograms are useful

energy at different frequencies

similar to how music is measured

in music theory you can measure distinct genres from their mel spectrograms

we can do this for wave types

but how do we classify the data

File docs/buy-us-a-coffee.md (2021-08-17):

---
description: This is what we do with our money.
---

# Buy us a coffee ☕

[https://www.buymeacoffee.com/t3chflicks](https://www.buymeacoffee.com/t3chflicks)

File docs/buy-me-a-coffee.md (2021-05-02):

---
description: This is what we do with our money.
---

# Buy me a coffee ☕

[https://www.buymeacoffee.com/t3chflicks](https://www.buymeacoffee.com/t3chflicks)

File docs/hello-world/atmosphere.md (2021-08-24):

# Atmosphere

What is atmosphere?

The Earth's atmosphere is the collection of gas particles which remain restrained by the Earth's gravitational field.



What are some things we can point to?



What systems are there?



How can we measure these systems?

What can our measurements tell us about these systems?





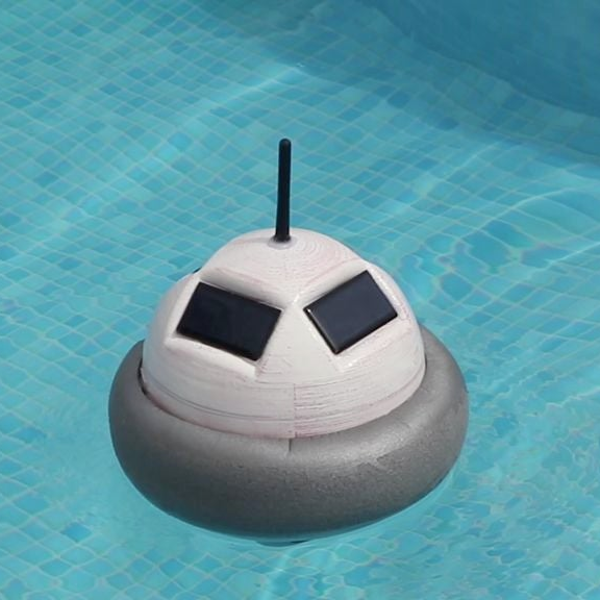
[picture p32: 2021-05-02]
docs/.gitbook/assets/smart-buoy-600.png

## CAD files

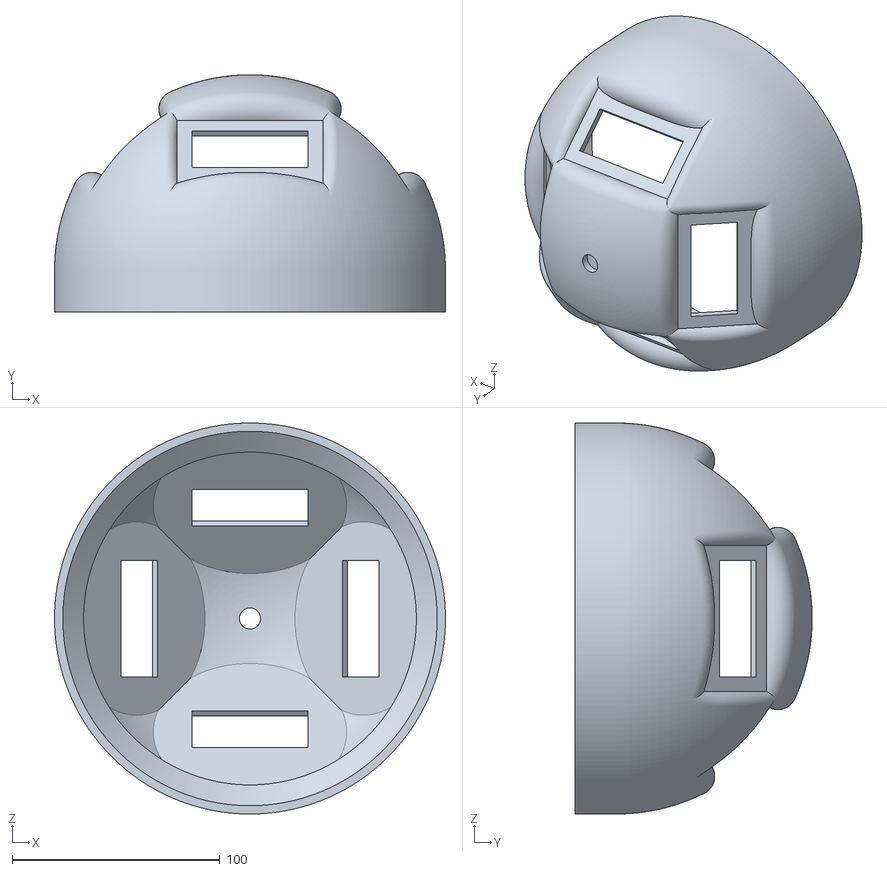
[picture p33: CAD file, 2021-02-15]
src/buoy/3d/top.stl
188.0 x 113.9 x 188.0

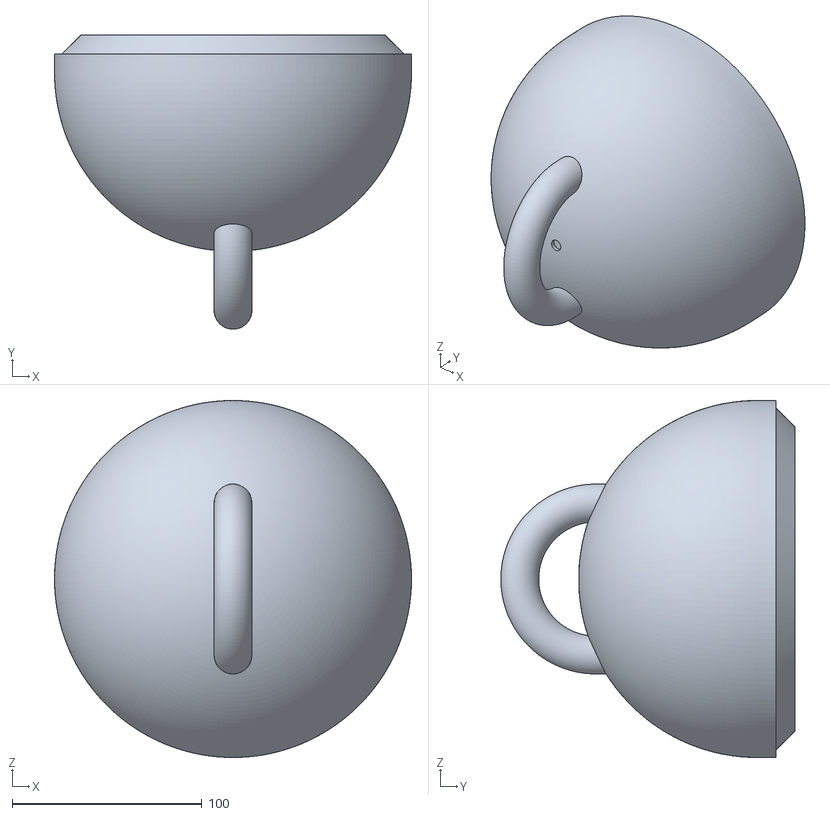
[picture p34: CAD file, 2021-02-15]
src/buoy/3d/bottom.stl
188.0 x 155.0 x 188.0

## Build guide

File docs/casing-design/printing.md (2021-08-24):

---
description: Practical help for those printing a buoy
---

# Printing

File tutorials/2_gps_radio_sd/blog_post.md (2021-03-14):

# Smart Buoy — GPS, Radio (NRF24) and a SD Card Module 📍📡💾

This Smart Buoy series charts our (ambitious) attempt to build a scientific buoy that can take meaningful measurements about the sea using off-the-shelf products. This is tutorial two of four — make sure you’re up to date, and if you need a swift introduction to the project, check out our summary.

[**Part 1**: Making wave and temperature measurements](https://t3chflicks.medium.com/smart-buoy-making-wave-and-temperature-measurements-%EF%B8%8F-cdda14c52196)

In this tutorial, we show show you how to get GPS data, store it on an SD card and send it somewhere using radio.

We did this so we could keep track of the location of our seaborne Buoy. The radio means that we can watch it remotely and the SD card means that on the off chance something breaks and it goes for a wander, we can download the data it collected during its unplanned excursion — if we’re ever able to retrieve it!



## Supplies

* GPS module — [Amazon](https://amzn.to/2jHgwJ2)

* SD card module — [Amazon](https://amzn.to/2SPbZBK)

* SD card — [Amazon](https://amzn.to/2SRhyiX)

* 2 X Radio modules (NRF24L01+) — [Amazon](https://amzn.to/2l6Fq5t)

* 2 X Arduino — [Amazon](https://amzn.to/2jJN7xR)
> # [🔗 Get The Smart Buoy Code On Github 📔](https://github.com/sk-t3ch/smart-buoy)

## Tutorial🤖

<center><iframe width='560' height='315' src ='https://www.youtube.com/embed/$xz1ix76U28E' frameborder='0' allowfullscreen></iframe></center>

### Getting GPS Data

The Smart Buoy takes sensor measurements as it sits in the sea, including GPS location and datetime. Take a look at the schematic below, which shows how we set up the circuit. The GPS module communicates via serial connection, so we used the Arduino software serial library as well as the tiny GPS library to communicate with it. These libraries (we’ll all be glad to hear) make everything super simple.



```c++
#include <TinyGPS++.h>
#include <SoftwareSerial.h>

TinyGPSPlus gps;
SoftwareSerial ss(4, 3);

struct dataStruct{
  double latitude;
  double longitude;
  unsigned long date;
  unsigned long time;
}gpsData;

void setup()
{
  Serial.begin(115200);
  ss.begin(9600);
}

void loop()
{
  while (ss.available() > 0){
    if (gps.encode(ss.read())){
      getInfo();
      printResults();
    }
  }
}

void getInfo(){
  if (gps.location.isValid()){
    gpsData.latitude = gps.location.lat();
    gpsData.longitude = gps.location.lng();
  }
  else{
    Serial.println("Invalid location");
  }
  if (gps.date.isValid()){
    gpsData.date = gps.date.value();
  }
  else{
    Serial.println("Invalid date");
  }
  if (gps.time.isValid()){
    gpsData.time = gps.time.value();
  }
  else{
    Serial.println("Invalid time");
  }
}

void printResults(){
  Serial.print("Location: ");
  Serial.print(gpsData.latitude, 6); Serial.print(", "); Serial.print(gpsData.longitude, 6);
  Serial.print("  Date: ");
  Serial.print(gpsData.date);
  Serial.print("  Time: ");
  Serial.print(gpsData.time);
  Serial.println();
}
```

### Sending GPS Data Via Radio

If the Buoy is out at sea taking measurements, there may be instances where we want to access its data without getting our feet wet or bringing it ashore. To get the measurements remotely, we used a radio module connected to an Arduino on both sides of the communication. In future, we hope to replace the receiver-side Arduino with a raspberry pi. The radio works similarly with both these interfaces, so swapping them over is pretty straightforward.

The radio module communicates using SPI, which requires a few more connections than I2C but is still really easy to use because of the NRF24 library. Using the GPS module for the sensor measurements, we transmitted its data from one Arduino to the other. We connected up the GPS and radio module to the Arduino and on the other side an Arduino with the radio module — have a look at the schematic.

## **Transmitter**



```c++
#include <SPI.h>
#include <nRF24L01.h>
#include <RF24.h>
#include <TinyGPS++.h>
#include <SoftwareSerial.h>

TinyGPSPlus gps;

SoftwareSerial ss(4, 3);
RF24 radio(8, 7); // CE, CSN

struct dataStruct{
  double latitude;
  double longitude;
  unsigned long date;
  unsigned long time;
}gpsData;

void setup() {
  Serial.begin(115200);
  ss.begin(9600);
  
  Serial.println("Setting up radio");
  //  Setup transmitter radio
  radio.begin();
  radio.openWritingPipe(0xF0F0F0F0E1LL);
  radio.setChannel(0x76);
  radio.setPALevel(RF24_PA_MAX);
  radio.setDataRate(RF24_250KBPS);
  radio.stopListening();
  radio.enableDynamicPayloads();
  radio.powerUp();
  Serial.println("Starting to send");
}

void loop() {
  while (ss.available() > 0){
    if (gps.encode(ss.read())){
      getInfo();
      radio.write(&gpsData, sizeof(gpsData));
    }
  }
} 

void getInfo(){
  if (gps.location.isValid()){
    gpsData.longitude = gps.location.lng();
    gpsData.latitude = gps.location.lat();
  }
  else{
    gpsData.longitude = 0.0;
    gpsData.latitude = 0.0;
  }
  if (gps.date.isValid()){
    gpsData.date = gps.date.value();
  }
  else{
    gpsData.date = 0;
  }
  if (gps.time.isValid()){
    gpsData.time = gps.time.value();
  }
  else{
    gpsData.time = 0;
  }
}
```

## **Receiver**



```c++
#include <SPI.h>
#include <nRF24L01.h>
#include <RF24.h>

RF24 radio(8, 7); // CE, CSN

struct dataStruct{
  double latitude;
  double longitude;
  unsigned long date;
  unsigned long time;
}gpsData;

void setup() {
  Serial.begin(115200);
  //  Setup receiver radio
  radio.begin();
  radio.openReadingPipe(1, 0xF0F0F0F0E1LL);
  radio.setChannel(0x76);
  radio.setPALevel(RF24_PA_MAX);
  radio.setDataRate(RF24_250KBPS);
  radio.startListening();
  radio.enableDynamicPayloads();
  radio.powerUp();
}

void loop() {
  if (radio.available()) {
    radio.read(&gpsData, sizeof(gpsData));
    Serial.print("Location: ");
    Serial.print(gpsData.latitude, 6);
    Serial.print(", ");
    Serial.print(gpsData.longitude, 6);
    Serial.print("  Date: ");
    Serial.print(gpsData.date);
    Serial.print("  Time: ");
    Serial.print(gpsData.time);
    Serial.println();

  }
} 
```

### Storing Data Using an SD Card Module

While the radio module was quite reliable, we decided it was best to have a built-in contingency in case there was a power cut on the receiver side, or the module moved out of range. Our contingency plan was an SD card module which allowed us to store the data collected. The quantity of data being collected wasn’t that large, so even a small SD card would easily be able to store a day’s worth of data.



```c++
#include <SPI.h>
#include <SD.h>
#include <TinyGPS++.h>
#include <SoftwareSerial.h>

TinyGPSPlus gps;

SoftwareSerial ss(4, 3);

struct dataStruct{
  double latitude;
  double longitude;
  unsigned long date;
  unsigned long time;
}gpsData;

void setup() {
  Serial.begin(115200);
  ss.begin(9600);
  
  if (!SD.begin(5)) {
    Serial.println("Card failed, or not present");
    return;
  }
  Serial.println("card initialized.");

  File dataFile = SD.open("gps_data.csv", FILE_WRITE);
  if (dataFile) {
    dataFile.println("Latitude, Longitude, Date, Time");
    dataFile.close();
  }
  else{
    Serial.println("nope cant open file");
  }
}

void loop() {
  while (ss.available() > 0){
    if (gps.encode(ss.read())){
      getInfo();
      printResults(); 
      saveInfo();
    }
  }
}

void getInfo(){
  if (gps.location.isValid()){
    gpsData.latitude = gps.location.lat();
    gpsData.longitude = gps.location.lng();
  }
  else{
    Serial.println("Invalid location");
  }
  if (gps.date.isValid()){
    gpsData.date = gps.date.value();
  }
  else{
    Serial.println("Invalid date");
  }
  if (gps.time.isValid()){
    gpsData.time = gps.time.value();
  }
  else{
    Serial.println("Invalid time");
  }
}

void printResults(){
  Serial.print("Location: ");
  Serial.print(gpsData.latitude, 6); Serial.print(", "); Serial.print(gpsData.longitude, 6);
  Serial.print("  Date: ");
  Serial.print(gpsData.date);
  Serial.print("  Time: ");
  Serial.print(gpsData.time);
  Serial.println();
}

void saveInfo(){
 File dataFile = SD.open("gps_data.csv", FILE_WRITE);
  if (dataFile) {
    dataFile.print(gpsData.latitude);
    dataFile.print(", ");
    dataFile.print(gpsData.longitude);
    dataFile.print(", ");
    dataFile.print(gpsData.date);
    dataFile.print(", ");
    dataFile.println(gpsData.time); 
    dataFile.close();
  }
  else{
    Serial.println("nope no datafile");
  }
}
```

Sadly, we had massive problems with the SD card. It just wouldn’t work, it caused us a lot of grief and in the end, we scrapped it. This meant we didn’t have a contingency plan…ah, the best laid plans…

### Sending and Storing GPS Data

To both send and store data, we had multiple [SPI](https://en.wikipedia.org/wiki/Serial_Peripheral_Interface) devices which attempted to communicate with the Arduino. The SPI protocol allows multiple devices to share the same MISO and MOSI and SCK connections and select a specific device using the ChipSelect (CS) connection per device. This is usually hidden from the user in most Arduino libraries.

The following code and circuits allow you to make GPS measurements and save them to an SD card whilst also sending to another Arudino via the radio module.

**Transmitter**



```c++
#include <SPI.h>
#include <nRF24L01.h>
#include <RF24.h>
#include <TinyGPS++.h>
#include <SoftwareSerial.h>
#include <SD.h>

TinyGPSPlus gps;

SoftwareSerial ss(4, 3);
RF24 radio(8, 7); // CE, CSN

struct dataStruct{
  double latitude;
  double longitude;
  unsigned long date;
  unsigned long time;
}gpsData;

void setup() {
  Serial.begin(115200);
  ss.begin(9600);

  //  Setup transmitter radio
  radio.begin();
  radio.openWritingPipe(0xF0F0F0F0E1LL);
  radio.setChannel(0x76);
  radio.setPALevel(RF24_PA_MAX);
  radio.setDataRate(RF24_250KBPS);
  radio.stopListening();
  radio.enableDynamicPayloads();
  radio.powerUp();

  if (!SD.begin(5)) {
    Serial.println("Card failed, or not present");
    return;
  }
  Serial.println("card initialized.");

  File dataFile = SD.open("gps_data.csv", FILE_WRITE);
  if (dataFile) {
    dataFile.println("Latitude, Longitude, Date, Time");
    dataFile.close();
  }
  else{
    Serial.println("nope cant open file");
  }
}

void loop() {
  while (ss.available() > 0){
    if (gps.encode(ss.read())){
      getInfo();
      sendInfo();
      saveInfo();
    }
  }
} 

void getInfo(){
  if (gps.location.isValid()){
    gpsData.latitude = gps.location.lat();
    gpsData.longitude = gps.location.lng();
  }
  else{
    Serial.println("Invalid location");
  }
  if (gps.date.isValid()){
    gpsData.date = gps.date.value();
  }
  else{
    Serial.println("Invalid date");
  }
  if (gps.time.isValid()){
    gpsData.time = gps.time.value();
  }
  else{
    Serial.println("Invalid time");
  }
}

void saveInfo(){
 File dataFile = SD.open("gps_data.csv", FILE_WRITE);
  if (dataFile) {
    dataFile.print(gpsData.latitude);
    dataFile.print(", ");
    dataFile.print(gpsData.longitude);
    dataFile.print(", ");
    dataFile.print(gpsData.date);
    dataFile.print(", ");
    dataFile.println(gpsData.time); 
    dataFile.close();
  }
  else{
    Serial.println("nope no datafile");
  }
}

void sendInfo(){
  radio.write(&gpsData, sizeof(gpsData));
}
```

## Thanks For Reading



Thanks for reading this tutorial, this has been the second step in building our Smart Buoy. Check out our next tutorial to see how we schedule power to the system using solar panels, 18650 batteries and RTC module timing circuits.

[**Part 1**: Making wave and temperature measurements](https://t3chflicks.medium.com/smart-buoy-making-wave-and-temperature-measurements-%EF%B8%8F-cdda14c52196)

[**Part 2**: GPS, Radio (NRF24) and SD Card Module](https://t3chflicks.medium.com/smart-buoy-gps-radio-nrf24-and-a-sd-card-module-6029af3a69d)

[**Part 3**: Scheduling Power to the Buoy](https://t3chflicks.medium.com/smart-buoy-scheduling-power-to-the-system-81a2675fdac0)

[**Part 4**: Waterproofing, Dashboards and Deploy!](https://t3chflicks.medium.com/smart-buoy-waterproofing-dashboards-and-deploy-15c730bf9a3a)

We hope you enjoyed this article. If you like the style, check out [T3chFlicks.org](https://t3chflicks.org/) for more tech-focused educational content as well as all the fun stuff we do on [YouTube](https://www.youtube.com/channel/UC0eSD-tdiJMI5GQTkMmZ-6w) ([Instagram](https://www.instagram.com/t3chflicks/), [Facebook](https://www.facebook.com/t3chflicks), [Twitter](https://twitter.com/t3chflicks)).

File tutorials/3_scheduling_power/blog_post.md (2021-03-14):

# Smart Buoy — Scheduling Power to the System🔋⌛

This Smart Buoy series charts our (ambitious) attempt to build a scientific buoy that can take meaningful measurements about the sea using off-the-shelf products. This is tutorial three of four— make sure you’re up to date, and if you need a swift introduction to the project, check out our summary.

[**Part 1**: Making wave and temperature measurements](https://t3chflicks.medium.com/smart-buoy-making-wave-and-temperature-measurements-%EF%B8%8F-cdda14c52196)

[**Part 2**: GPS, Radio (NRF24) and SD Card Module](https://t3chflicks.medium.com/smart-buoy-gps-radio-nrf24-and-a-sd-card-module-6029af3a69d)

In this tutorial, we move onto the next challenge in our Smart Buoy project: how to control the power for it!

We didn’t need the Buoy to constantly take measurements — a few at regular intervals was plenty. Intermittent operation does make powering it slightly easier, because it can be off occasionally.

Another thing which simplified the powering process was the small size of the Buoy and its sensors, meaning we were able to use small, low power solar panels. However, this meant we needed to manage the little power we had effectively, to ensure the Buoy could take regular measurements throughout the day. We decided that we wanted to schedule the power to the Buoy based on how much energy there was in the battery.



## Supplies

* 18650 Battery —[Amazon](https://amzn.to/2ZOMuCq)

* Buck booster — [Amazon](https://amzn.to/2ZS1a3q)

* Charge controller — [Amazon](https://amzn.to/2ZS1a3q)

* Solar panel —[ Amazon](https://amzn.to/2ZS1a3q)

* Blocking diodes — [Amazon](https://amzn.to/2ZS1a3q)

* Power monitoring module —[Amazon](https://amzn.to/2ZS1a3q)

* Real time clock —[Amazon](https://amzn.to/2ZS1a3q)

* Arduino — [Amazon](https://amzn.to/2ZS1a3q)

* P-channel transistor — [Amazon](https://amzn.to/2ZS1a3q)
> # [🔗 Get The Smart Buoy Code On Github 📔](https://github.com/sk-t3ch/smart-buoy)

## Tutorial 🤖

### Powering the Buoy

We powered the Smart Buoy using a 18650 battery, which was charged by four, 5V, 60mA solar panels in parallel. In our design, the four solar panels sit around the top of the Buoy, capturing maximum sunlight.

We put in some blocking diodes to prevent reverse current into the panels.
We used a charge controller to control the battery output and charge from the solar panels. The charge controller output isn’t high enough to power the system stably, so we used a buck booster to increase the voltage to about 6V.

As a solely solar-powered device, it’s unlikely the Buoy would make it through the night with enough power to continue taking measurements. To ensure it always had enough power to operate the sensors, we used a real time clock module to turn the system on and off. This module was battery operated, but used such a low amount of current it could run for years.

We programmed the real time clock module to have an alarm, set based on how much power is in the battery. This value was inferred based on the battery voltage which was measured using a power monitor module. When the alarm was triggered, it changed the alarm pin from high to low. We used this to turn on a transistor, which allowed power to the arduino. The system then took its measurements and turned off by clearing the alarm and changing the pin back to high, which turned the transistor off.







### Controlling Power Using the RTC Alarms

Here’s an example of how to programme an alarm to control power to the Arduino. In this example, we demonstrate using an Arduino to turn on an LED for three seconds, set an alarm for 15 seconds and then turn itself off. Once 15 seconds have passed, the alarm triggers, the LED turns on again and the cycle repeats.



```c++
#include <DS3232RTC.h>
#include <Wire.h> 

int led = LED_BUILTIN; 

void setup() {
  Serial.begin(115200);
  Wire.begin();
  pinMode(led, OUTPUT);
}

void loop() {
  
  digitalWrite(led, HIGH);
  delay(3000);
  reset_alarm();
}

void reset_alarm(){
  Wire.beginTransmission(0x70);
  Wire.write(1 << 6);
  Wire.endTransmission();
  RTC.alarmInterrupt(ALARM_1, true); // alarm is an output trigger
  RTC.squareWave(SQWAVE_NONE);
  //      0h 0m 0s 
  setTime(0, 0, 0, 1, 1, 1970); 
  RTC.set(now());
  // set new alarm
  RTC.setAlarm(ALM1_MATCH_SECONDS, 15, 0, 0, 1);
  // clear old alarm flag - turning off system
  RTC.alarm(ALARM_1);
}
```

### Monitoring Power

This is how we monitored battery voltage and current usage using the INA219 DC current monitor. This module communicates using I²C — refer to the schematic for the connections. A nice library for talking to the module already exists, which made this process really easy.



```c++
#include <Wire.h>
#include <Adafruit_INA219.h>

Adafruit_INA219 ina219;
float shuntvoltage = 0;
float busvoltage = 0;
float current_mA = 0;
float loadvoltage = 0;
float power_mW = 0;

void setup() {
  Serial.begin(115200);
  while (!Serial) {
      delay(1);
  }
  ina219.begin();
  ina219.setCalibration_32V_1A();
}

void loop() {
  shuntvoltage = ina219.getShuntVoltage_mV();
  busvoltage = ina219.getBusVoltage_V();
  current_mA = ina219.getCurrent_mA();
  power_mW = ina219.getPower_mW();
  loadvoltage = busvoltage + (shuntvoltage / 1000);
  Serial.print("Load Voltage:  "); Serial.print(loadvoltage); Serial.println(" V");
  Serial.print("Current:       "); Serial.print(current_mA);  Serial.println(" mA");
  Serial.print("Power:         "); Serial.print(power_mW);    Serial.println(" mW");
  Serial.println();
  delay(1000);
}
```

## Using the Power Monitor to Set the Next RTC Alarm

Finally, this is how we used the voltage to predict the optimal duration between alarms. The method was a bit crude — if anyone has any better ideas, please get in touch!



```c++
#include <DS3232RTC.h>
#include <Adafruit_INA219.h>
#include <Wire.h> 

int led = LED_BUILTIN; 

// INA219 - Power Monitor
Adafruit_INA219 ina219;

void setup() {
  Wire.begin();
  pinMode(led, OUTPUT);
  
  // initialise INA219 - Power Monitor
  ina219.begin();
  ina219.setCalibration_32V_1A();
}

void loop() {
  digitalWrite(led, HIGH);
  delay(3000);
  reset_alarm();
}

void reset_alarm(){
  RTC.alarmInterrupt(ALARM_1, true);
  RTC.squareWave(SQWAVE_NONE);
  setTime(0, 0, 0, 0, 0, 1970); 
  RTC.set(now());
  int wait_time = get_wait_time_from_voltage();
  // set new alarm
  RTC.setAlarm(ALM1_MATCH_MINUTES, 0, wait_time, 0, 0);
  // clear old alarm flag - turning off system
  RTC.alarm(ALARM_1);
}

int get_wait_time_from_voltage(){
  float shuntvoltage = ina219.getShuntVoltage_mV();
  float busvoltage = ina219.getBusVoltage_V();
  float loadvoltage = busvoltage + (shuntvoltage / 1000);

  // Samsung 18650 % capacity at a given voltage
  // batt_voltages            0.0, 3.4, 3.5, 3.6, 3.7, 3.8, 3.9, 4.0, 4.1, 4.2, 4.5
  // batt_percentages           0,   0,   9,  22,  52,  64,  75,  84,  93, 100, 100
  int wait_time;
  if (loadvoltage < 3.6) wait_time = 55;
  else if (loadvoltage < 3.8) wait_time = 25;
  else if (loadvoltage < 4.0) wait_time = 15;
  else if (loadvoltage < 4.1) wait_time = 10;
  else wait_time = 3;
  
  return wait_time;
}
```
> # [🔗 Get The Smart Buoy Code On Github 📔](https://github.com/sk-t3ch/smart-buoy)

## Thanks for reading



Thanks for reading this tutorial. This has been the third step in building our Smart Buoy, check out our next tutorial to see how we built the Buoy and base station, and deployed it to the (drumroll please) ocean…

[**Part 1**: Making wave and temperature measurements](https://t3chflicks.medium.com/smart-buoy-making-wave-and-temperature-measurements-%EF%B8%8F-cdda14c52196)

[**Part 2**: GPS, Radio (NRF24) and SD Card Module](https://t3chflicks.medium.com/smart-buoy-gps-radio-nrf24-and-a-sd-card-module-6029af3a69d)

[**Part 3**: Scheduling Power to the Buoy](https://t3chflicks.medium.com/smart-buoy-scheduling-power-to-the-system-81a2675fdac0)

[**Part 4**: Waterproofing, Dashboards and Deploy!](https://t3chflicks.medium.com/smart-buoy-waterproofing-dashboards-and-deploy-15c730bf9a3a)

We hope you enjoyed this article. If you like the style, check out [T3chFlicks.org](https://t3chflicks.org/) for more tech-focused educational content as well as all the fun stuff we do on [YouTube](https://www.youtube.com/channel/UC0eSD-tdiJMI5GQTkMmZ-6w) ([Instagram](https://www.instagram.com/t3chflicks/), [Facebook](https://www.facebook.com/t3chflicks), [Twitter](https://twitter.com/t3chflicks)).

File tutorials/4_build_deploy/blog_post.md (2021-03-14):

# Smart Buoy — Waterproofing, Dashboards and Deploy 🚱📊

This Smart Buoy series charts our (ambitious) attempt to build a scientific buoy that can take meaningful measurements about the sea using off-the-shelf products. This is our final tutorial— make sure you’re up to date, and if you need a swift introduction to the project, check out our summary.

[**Part 1**: Making wave and temperature measurements](https://t3chflicks.medium.com/smart-buoy-making-wave-and-temperature-measurements-%EF%B8%8F-cdda14c52196)

[**Part 2**: GPS, Radio (NRF24) and SD Card Module](https://t3chflicks.medium.com/smart-buoy-gps-radio-nrf24-and-a-sd-card-module-6029af3a69d)

[**Part 3**: Scheduling Power to the Buoy](https://t3chflicks.medium.com/smart-buoy-scheduling-power-to-the-system-81a2675fdac0)

In this article, we show you how we designed the casing to protect our Smart Buoy from water, waves and shark attacks. We also explain how we connected it to the base station, which hosted a database and interactive dashboard to explore data in real time.



## Supplies

As this is the final stage for the project, you’re going to need **ALL** the supplies:

* Arduino Nano — [Amazon](https://amzn.to/2jJN7xR)

* Raspberry Pi Zero — [Amazon](https://amzn.to/2jHpV3D)

* Battery (18650) — [Amazon](https://amzn.to/2ld11cp)

* Solar panels — [Amazon](https://amzn.to/2ld2vmZ)

* Blocking Diodes — [Amazon](https://amzn.to/2ld2X4F)

* Charge controller — [Amazon](https://amzn.to/2jJhRz0)

* Buck booster — [Amazon](https://amzn.to/2jFnCxX)

* GPS module — [Amazon](https://amzn.to/2jHgwJ2)

* GY-86 (accelerometer, gyroscope, barometer, compass) — [Amazon](https://amzn.to/2ld5bB3)

* Water Temperature sensor — [Amazon](https://amzn.to/2lbTASO)

* Power monitor module — [Amazon](https://amzn.to/2lbU5MG)

* Real time clock module — [Amazon](https://amzn.to/2ld6yjb)

* Radio modules — [Amazon](https://amzn.to/2l6Fq5t)

* i²c multiplexer module — [Amazon](https://amzn.to/2jJnP2S)

* 3D printer — [Amazon](https://amzn.to/2ld7xQp)

* PETG filament — [Amazon](https://amzn.to/30yw95r)

* Epoxy — [Amazon](https://amzn.to/2lbVRNQ)

* Primer spray paint — [Amazon](https://amzn.to/2ld55cE)

* Rope — [Amazon](https://amzn.to/2jHkjWM)

* Floats — [Amazon](https://amzn.to/2lfTZ6R)

* Glue — [Amazon](https://amzn.to/2jFpeaZ)
> # [🔗 Get The Smart Buoy Code On Github 📔](https://github.com/sk-t3ch/smart-buoy)

## Tutorial 🤖

<center><iframe width='560' height='315' src ='https://www.youtube.com/embed/$yUjocnaKXys' frameborder='0' allowfullscreen></iframe></center>

### Casing — Buoy

When we designed the Buoy, we had a couple of key things in mind: it needed to fit all the electronics inside, have slots for the solar panels, radio aerial and water temperature sensor. It also needed(!!) to be watertight and float. It also required an anchor point, so it wouldn’t just float away.

We used Autodesk Fusion 360 software to design the Buoy and we’re pretty happy with how it turned out. However, we shot ourselves in the foot slightly by not including a sealable slot for programming the Arduino, and were at the mercy of getting everything working perfectly before we glued it together.



### Casing — Base station

The Buoy communicated via radio and the messages were received by a base station. In the previous tutorials, we used the radio module with an Arduino for simplicity. The base station used a Raspberry Pi, which connected in the same way but allowed for much more processing.

There are many great open source cases on [Thingiverse](https://www.thingiverse.com/thing:1595429), including this [one](https://www.thingiverse.com/thing:1595429) that prints in one piece and has cut outs for wiring.

One Piece Raspberry Pi Zero Case — [Source](https://www.thingiverse.com/thing:1595429)*

One Piece Raspberry Pi Zero Case — [Source](https://www.thingiverse.com/thing:1595429)*

### Print — Buoy

3D printing is great fun but also time consuming and rage-inducing. Luckily, however, some people are much more experienced than we were and were quite helpful. Thanks to reddit user `@dbcottonhead`, we looked into PETG filament, which is meant to be much more durable and creates stronger shells. These are important things to take into account when making something that is expected to float in a salty sea in 40°C sun, while possibly smashing into some rocks…

To ensure waterproofing, our main focus was on layer adhesion:

* Thin layer heights of 0.3mm helped reduce the size of gaps

* 4 perimeters to reduce possibility of gaps and give wall strength

A completely solid Buoy would be watertight, but it also wouldn't float as the density of PETG is higher than that of water. We chose to have a 15% infill on the print.

Each half took around 24 hours to print and used 500g of PETG. The finished print was quite smooth, but with the stringiness and blobs you would expect when using PETG with FDM printing.



### Post-production

Even with careful initial planning and our attempts to improve layer adhesion, the Buoy wasn’t watertight. We started our post-production processing by sanding with various layers of quite rough grit.



We then sprayed over this uniformly rough surface with a few coats of plastic filler primer paint to fill the gaps.



This improved the outer shell, but did not completely remove layer gaps.



The final resort was to add a few coats of Epoxy resin. Epoxy is very durable and gave the Buoy a slight shine.



### Solar Panels

The Smart Buoy featured four solar panels equally spaced around its circumference. Each cell was capable of producing 5V at 60mA. A typical Arduino nano requires ~20mA, so we hoped this would be fine for our system. We soldered wires to the rear of the solar panels and connected to the rest of charging system.



We threaded the wires through and then glued the solar panels into water-tight position.



### Motherboard — Perfboard

With a lot of determination, solder, and wire, we connected the electronics together on perfboard.



We pushed the radio aerial and water temperature sensors through their respective holes and glued them into position.



The perfboard slotted neatly into the Buoy and we glued it into position.



As we mentioned in tutorial two, we removed the SD card module because it was causing massive headaches.

### Buoyancy

Logic (and probably science) dictated that the Buoy would float if it was less dense than the water. We believed the Buoy would float. But we didn’t have much trust in its stability.

Many of the buoys available to buy on the market are built such that they are self-righting. We opted for cutting a piece of pipe insulation and sticking it around the circumference of the middle of the Buoy. This had the bonus effect of making the Buoy look UFO-esque, and also potentially offered a bit of protection if any boats decided they wanted a closer look.



### Base Station

With all the sensors on board the Buoy, we were able to measure: wave height, wave period, wave power, water temperature, air temperature, air pressure, voltage, current usage and location. These values were sent from the Buoy to the Base Station using the radio modules.



We would have loved to measure wave direction and we were super close to making it work, but it was a massive struggle (have a look at [tutorial one](https://t3chflicks.medium.com/smart-buoy-making-wave-and-temperature-measurements-%EF%B8%8F-cdda14c52196) to see our pain and confusion in more detail) so in the end we ditched it (please help ❤).



### Dashboard

The Smart Buoy dashboard frontend was created using [VueJs](https://vuejs.org/). We won’t explain is great depth how we did this, but we can show you how to get it going. Detailed steps can be found in the [Github repo](https://github.com/sk-t3ch/smart-buoy/tree/master/src/server).

* SSH into the Raspberry Pi base station

* Install dependencies and create DB

* Download code and the configuration file`env.json`

* Add Raspberry Pi IP address and Google Maps Key

* Start the server

Once the base station begins radio communication with the Buoy, messages are stored in the database as well as streamed users of the real-time dashboard. Navigating to the dashboard **home** page in your browser, you should see the data streaming in.



The time series of measurements can be viewed simply by toggling the view control on each measurement card. If you want a closer look at the data, the **trends** page features a graphing tool, which queries the database running on the base station.



### Place — Where to put it?

Grenada is a wonderful island in the South Caribbean. The east coast, which faces the Atlantic, typically receives more wave energy than more sheltered western side. The tidal range (distance between high and low tide) is small, meaning the effects of sea level rise are more acutely felt. The increasing frequency and intensity of tropical storms in the Caribbean also poses a worrying threat, and major storms can cause significant damage to coastal areas.

Anyway, enough of that. We looked for somewhere to initially deploy the Buoy, taking into account our knowledge of the island and its coastal regions. An ideal spot needed small but dynamic waves, few rogue fisherman, and be easy for to access… So we initially tested in the pool.

Test Location — Pool*

Test Location — Pool*

While in Grenada, we also had the chance to talk with a friend who owns a beachfront dive shop. He has his own environmental mission — to create an artificial coral reef — which you can read more about [here](https://theecologist.org/2019/aug/19/saving-caribbean-corals-concrete). We were delighted when he gave us permission to attach our Buoy to one of this lines.

We anchored the Buoy to some others by knotting a piece of rope around the bottom side hook (yes, we’re pretty legit). It didn’t sink. IT WORKED!

Test Location — Sea*

Test Location — Sea*

## V2

The Smart Buoy project has been a great source of learning. We are very happy with the system we have managed to create, especially considering the (self-imposed) time and cost constraints.

However, the Buoy’s purpose was to take meaningful ocean measurements. We only managed to get the Buoy working a few days before we had to leave sunny Grenada. Back in the UK, the seaside is slightly less alluring…Not to say this project won’t continue. We’ve learned a lot, and now we can apply these improvements and hopefully go on another wonderful journey.

### Top Improvements

* Ability to open and reseal the Buoy

* LoRa ESP32 to replace Arduino in Buoy

* Data processing on wave measurements on the Buoy

## Thanks for Reading



[**Part 1**: Making wave and temperature measurements](https://t3chflicks.medium.com/smart-buoy-making-wave-and-temperature-measurements-%EF%B8%8F-cdda14c52196)

[**Part 2**: GPS, Radio (NRF24) and SD Card Module](https://t3chflicks.medium.com/smart-buoy-gps-radio-nrf24-and-a-sd-card-module-6029af3a69d)

[**Part 3**: Scheduling Power to the Buoy](https://t3chflicks.medium.com/smart-buoy-scheduling-power-to-the-system-81a2675fdac0)

[**Part 4**: Waterproofing, Dashboards and Deploy!](https://t3chflicks.medium.com/smart-buoy-waterproofing-dashboards-and-deploy-15c730bf9a3a)

We hope you enjoyed this article. If you like the style, check out [T3chFlicks.org](https://t3chflicks.org/) for more tech-focused educational content as well as all the fun stuff we do on [YouTube](https://www.youtube.com/channel/UC0eSD-tdiJMI5GQTkMmZ-6w) ([Instagram](https://www.instagram.com/t3chflicks/), [Facebook](https://www.facebook.com/t3chflicks), [Twitter](https://twitter.com/t3chflicks)).

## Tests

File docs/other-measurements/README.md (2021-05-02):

# Other Measurements

* Temperatures
* Air pressure
* humidity
* sea oxygen
* sea salt - conductivity
* sea pH
*

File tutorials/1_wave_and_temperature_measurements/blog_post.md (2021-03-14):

# Smart Buoy — Making Wave and Temperature Measurements 🌊🌡️

This Smart Buoy series charts our (ambitious) attempt to build a scientific buoy that can take meaningful measurements about the sea using off-the-shelf products. This is tutorial one of four. If you need a swift introduction to the project, check out our summary.

In this tutorial, we show you how we took wave and temperature measurements on our Smart Buoy. Be warned, this tutorial is pretty code-heavy, so if you’re here for a good time not for a long time, check out our [summary](https://www.youtube.com/watch?v=S-XMT6GDWk8&t=1s) first to get a nice brief overview before enjoying this in-depth look.



## Supplies

* Arduino Nano — [Amazon](https://amzn.to/2jJN7xR)

* GY-86 (accelerometer, gyroscope, barometer, compass) — [Amazon](https://amzn.to/2ld5bB3)

* Water Temperature sensor — [Amazon](https://amzn.to/2lbTASO)
> # [🔗 Get The Smart Buoy Code On Github 📔](https://github.com/sk-t3ch/smart-buoy)

## Tutorial 🤖

<center><iframe width='560' height='315' src ='https://www.youtube.com/embed/$AUr0UcNb6B8' frameborder='0' allowfullscreen></iframe></center>

### Accelerometer & Gyroscope



The main sensor on the buoy is a GY-86, which contains the MPU6050 accelerometer gyroscope, the HMC5883L Magnetometer and the MS5611 barometer. These sensors enable us to measure air temperature, wave height, wave period and wave energy (and wave direction if someone out there is smart enough to help us with the maths).

The GY-86 communicates via i2C — see the schematic. This is the code we used to access the accelerometer and gyroscope readings.

```c++
#include "Wire.h"
#include "I2Cdev.h" //   Get these libraries from https://github.com/jrowberg/i2cdevlib/tree/master/Arduino
#include "MPU6050.h" //  ^

MPU6050 mpu;

int16_t ax, ay, az;
int16_t gx, gy, gz;

void setup() {
  Serial.begin(115200);
  Wire.begin();
  Serial.println("Initializing MP6050...");
  mpu.initialize();
  Serial.println(mpu.testConnection() ? "MPU6050 connection successful" : "MPU6050 connection failed");

}

void loop() {
  mpu.getMotion6(&ax, &ay, &az, &gx, &gy, &gz);
  printResults();
  delay(10);
}

void printResults(){
  Serial.print("Acc (x,y,z) m/s/s: "); 
  Serial.print(ax); Serial.print(" "); 
  Serial.print(ay); Serial.print(" "); 
  Serial.print(az);
  Serial.print(" Gyro(x,y,z) °/s: "); 
  Serial.print(gx); Serial.print(" "); 
  Serial.print(gy); Serial.print(" "); 
  Serial.println(gz);
}
```

### Magnetometer (Compass)

The GY-86 contains a magnetometer which we used as a compass. You don’t need to change any connections — woo! The code to get the compass value is available below.

Remember to use the value of declination specific for your location, otherwise your results may be inaccurate.

```c++
#include "Wire.h"
#include "I2Cdev.h" //   Get these libraries from https://github.com/jrowberg/i2cdevlib/tree/master/Arduino
#include "MPU6050.h" //  ^
#include "HMC5883L.h" // ^
 
MPU6050 mpu;
HMC5883L mag;

int16_t mx, my, mz;

// Find the declination where you are from http://www.magnetic-declination.com
//                  -14°     59'            
float declination = (-14.0 - (59.0 / 60.0)) * (PI/180); 

void setup() {
  Serial.begin(115200);
  Wire.begin();
  Serial.println("Initializing I2C devices...");
  mpu.setI2CMasterModeEnabled(false);
  mpu.setI2CBypassEnabled(true) ;
  mpu.setSleepEnabled(false);
  mpu.initialize();
  mag.initialize();
  Serial.println(mpu.testConnection() ? "MPU6050 connection successful" : "MPU6050 connection failed");
  Serial.println(mag.testConnection() ? "HMC5883L connection successful" : "HMC5883L connection failed");

}

void loop() {
  mag.getHeading(&mx, &my, &mz);
  printResults();
  delay(200);
}

void printResults(){
  float heading = atan2(my, mx);
  heading += declination;
  if (heading < 0) heading += 2 * PI;
  if (heading > 2 * PI) heading -= 2 * PI;
  heading *= 180/M_PI;
  
  Serial.print("Heading °:"); 
  Serial.println(heading);
}

```

### Barometer and Temperature

Here’s how to get the values from the MS5611 barometer.

```c++
#include "Wire.h"
#include "I2Cdev.h" //   Get these libraries from https://github.com/jrowberg/i2cdevlib/tree/master/Arduino
#include "MPU6050.h" //  ^
#include <MS5611.h> // Get this library from https://github.com/jarzebski/Arduino-MS5611

MPU6050 mpu;
MS5611 baro;

double temp;
long pressure;
double altitude;

void setup() {
  Serial.begin(115200);
  Wire.begin();
  Serial.println("Initializing I2C devices...");
  mpu.setI2CMasterModeEnabled(false);
  mpu.setI2CBypassEnabled(true) ;
  mpu.setSleepEnabled(false);
  mpu.initialize();
  Serial.println(mpu.testConnection() ? "MPU6050 connection successful" : "MPU6050 connection failed");
  while (!baro.begin(MS5611_ULTRA_HIGH_RES)) {
    Serial.println("MS5611 connection unsuccessful, check wiring!");
    delay(500);
  }
}

void loop() {
  temp = baro.readTemperature(true);
  pressure = baro.readPressure(true);
  altitude = baro.getAltitude(pressure);
  printResults();
  delay(200);
}

void printResults(){
  Serial.print("Pressure hPa: "); Serial.print(pressure);
  Serial.print("  Altitude m: "); Serial.print(altitude);
  float tempC = temp / 340.00 + 36.53;
  Serial.print("  Temp °C: "); Serial.println(tempC);
}
```

### [Crude] Wave Height

Once all those sensors are set up, you can use them to measure wave properties, starting with wave height…

The altitude of the Buoy can be calculated using air pressure. We used the relative altitude of the Buoy over a time period to work out the wave height like this:

```c++
#include "Wire.h"
#include "I2Cdev.h" //   Get these libraries from https://github.com/jrowberg/i2cdevlib/tree/master/Arduino
#include "MPU6050.h" //  ^
#include <MS5611.h> // Get this library from https://github.com/jarzebski/Arduino-MS5611

MPU6050 mpu;
MS5611 baro;

long pressure;
double altitude, min_height, max_height, wave_height;

void setup() {
  Serial.begin(115200);
  Wire.begin();
  Serial.println("Initializing I2C devices...");
  mpu.setI2CMasterModeEnabled(false);
  mpu.setI2CBypassEnabled(true) ;
  mpu.setSleepEnabled(false);
  mpu.initialize();
  Serial.println(mpu.testConnection() ? "MPU6050 connection successful" : "MPU6050 connection failed");
  while (!baro.begin(MS5611_ULTRA_HIGH_RES)) {
    Serial.println("MS5611 connection unsuccessful, check wiring!");
    delay(500);
  }
}

void loop() {
  unsigned long start_time = millis();
  pressure = baro.readPressure(true);
  altitude = baro.getAltitude(pressure);
  max_height = altitude;
  min_height = altitude;

  //  for 5 seconds
  while(millis() - start_time < 5000){
    pressure = baro.readPressure(true);
    altitude = baro.getAltitude(pressure);
    if (altitude < min_height) min_height = altitude;
    if (altitude > max_height) max_height = altitude;
  }
  wave_height = (max_height - min_height)/2.0;
  Serial.print("Wave Height m: "); Serial.println(wave_height);
}
```

### [Crude] Wave Period

Next, wave period. We used airy wave theory — a lovely basic wave theory which says that water surface waves can be described as sine waves. It’s great to use because it makes the maths easier, but it is of course a simplification and does have certain caveats, including that it is inaccurate in shallower water where waves transform and break.

Using the midpoint between our maximum and minimum relative altitudes and finding how frequently the Buoy crossed this point, we figured we would be able to get a value for wave period.

```c++
#include "Wire.h"
#include "I2Cdev.h" //   Get these libraries from https://github.com/jrowberg/i2cdevlib/tree/master/Arduino
#include "MPU6050.h" //  ^
#include <MS5611.h> // Get this library from https://github.com/jarzebski/Arduino-MS5611

MPU6050 mpu;
MS5611 baro;

long pressure;
double altitude, min_height, max_height, mid_point, smudge_factor;
byte escaped, started;
unsigned long period_start, period_end;
float avg_period = -1;

void setup() {
  Serial.begin(115200);
  Wire.begin();
  Serial.println("Initializing I2C devices...");
  mpu.setI2CMasterModeEnabled(false);
  mpu.setI2CBypassEnabled(true) ;
  mpu.setSleepEnabled(false);
  mpu.initialize();
  Serial.println(mpu.testConnection() ? "MPU6050 connection successful" : "MPU6050 connection failed");
  while (!baro.begin(MS5611_ULTRA_HIGH_RES)) {
    Serial.println("MS5611 connection unsuccessful, check wiring!");
    delay(500);
  }
}

void loop() {
  unsigned long start_time = millis();
  pressure = baro.readPressure(true);
  altitude = baro.getAltitude(pressure);
  max_height = altitude;
  min_height = altitude;

  //  for 5 seconds
  while(millis() - start_time < 5000){
    pressure = baro.readPressure(true);
    altitude = baro.getAltitude(pressure);
    if (altitude < min_height) min_height = altitude;
    if (altitude > max_height) max_height = altitude;
  }
  mid_point = (max_height + min_height)/2.0;
  smudge_factor = (max_height - mid_point)*0.15;
  Serial.print("Mid Point m: "); Serial.print(mid_point);
  
  start_time = millis();
  //  for 5 seconds 
  while(millis() - start_time < 5000){
    pressure = baro.readPressure(true);
    altitude = baro.getAltitude(pressure);
    //    if within a range of 30% of wave height from the mid point
    //    start the timer else stop it
    if (altitude < mid_point + smudge_factor && altitude > mid_point - smudge_factor){
      if ( !started){
        period_start = millis();
        started = true;
      }
      else{
        if ( escaped ){
          // if it has started and escaped and is now returning
          period_end = millis();
          started = false;
          escaped = false;
          // if the variable has already been assigned
          // use its previous value and new value to work out avg
          if(avg_period != -1){
            avg_period = (avg_period + (period_end-period_start)*2)  / 2.0;
          }
          // assign it
          else{
            avg_period =  (period_end-period_start)*2; 
          }

        }
      }
    }
    else{
      escaped = true;
    } 
  }
  Serial.print("  Period s: "); Serial.println(avg_period/1000);
}

```

### Wave Direction (HELP!)

We never actually managed to measure wave direction.

However, the sensors aboard the Buoy *should *be able to do it. It is possible to measure dynamic accelerations with the GY-86 Accelerometer by subtracting the affects of the gravitational force. It is also possible to get the direction of this acceleration. Using the direction of Buoy acceleration, along with the compass value for a given position, should allow you to determine wave direction. We gave it a go in the code below.
> If someone out there could help us with this it would be amazing ❤

```c++
#include "I2Cdev.h"
#include "MPU6050_6Axis_MotionApps20.h"
#include "HMC5883L.h"
#include "Wire.h"
MPU6050 mpu;
HMC5883L mag;

int16_t mx, my, mz;

#define INTERRUPT_PIN 2  // use pin 2 on Arduino Uno & most boards
float declination = -14.0 - (59.0 / 60.0);

// MPU control/status vars
bool dmpReady = false;  // set true if DMP init was successful
uint8_t mpuIntStatus;   // holds actual interrupt status byte from MPU
uint8_t devStatus;      // return status after each device operation (0 = success, !0 = error)
uint16_t packetSize;    // expected DMP packet size (default is 42 bytes)
uint16_t fifoCount;     // count of all bytes currently in FIFO
uint8_t fifoBuffer[64]; // FIFO storage buffer

// orientation/motion vars
Quaternion q;           // [w, x, y, z]         quaternion container
VectorInt16 aa;         // [x, y, z]            accel sensor measurements
VectorInt16 aaReal;     // [x, y, z]            gravity-free accel sensor measurements
VectorInt16 aaWorld;    // [x, y, z]            world-frame accel sensor measurements
VectorFloat gravity;    // [x, y, z]            gravity vector
volatile bool mpuInterrupt = false;     // indicates whether MPU interrupt pin has gone high
void dmpDataReady() {
    mpuInterrupt = true;
}

void setup() {
    Serial.begin(115200);
    Wire.begin();
    Wire.setClock(400000); 
    
    mpu.setI2CMasterModeEnabled(false);
    mpu.setI2CBypassEnabled(true) ;
    mpu.setSleepEnabled(false);
    mpu.initialize();
    mag.initialize();
   // initialize device
    Serial.println(F("Initializing I2C devices..."));
    mpu.initialize();
    pinMode(INTERRUPT_PIN, INPUT);
    Serial.println(mpu.testConnection() ? F("MPU6050 connection successful") : F("MPU6050 connection failed"));
devStatus = mpu.dmpInitialize();
  // supply your own gyro offsets here, scaled for min sensitivity
    mpu.setXGyroOffset(112);
    mpu.setYGyroOffset(5);
    mpu.setZGyroOffset(-15);
    mpu.setZAccelOffset(1487); 
    if (devStatus == 0) {
        mpu.setDMPEnabled(true);
        Serial.print(digitalPinToInterrupt(INTERRUPT_PIN));
        attachInterrupt(digitalPinToInterrupt(INTERRUPT_PIN), dmpDataReady, RISING);
        mpuIntStatus = mpu.getIntStatus();
        dmpReady = true;
        packetSize = mpu.dmpGetFIFOPacketSize();
    }

}

void loop() {
    if (!dmpReady) return;
    while (!mpuInterrupt && fifoCount < packetSize) {
        if (mpuInterrupt && fifoCount < packetSize) {
          fifoCount = mpu.getFIFOCount();
        }        
    }       
    mpuInterrupt = false;
    mpuIntStatus = mpu.getIntStatus();
    fifoCount = mpu.getFIFOCount();
    if ((mpuIntStatus & _BV(MPU6050_INTERRUPT_FIFO_OFLOW_BIT)) || fifoCount >= 1024) {
        mpu.resetFIFO();
        fifoCount = mpu.getFIFOCount();
    } 
    else if (mpuIntStatus & _BV(MPU6050_INTERRUPT_DMP_INT_BIT)) {
        while (fifoCount < packetSize) fifoCount = mpu.getFIFOCount();
        mpu.getFIFOBytes(fifoBuffer, packetSize);
        fifoCount -= packetSize;

      // OUTPUT_READABLE_WORLDACCEL
      mpu.dmpGetQuaternion(&q, fifoBuffer);
      mpu.dmpGetAccel(&aa, fifoBuffer);
      mpu.dmpGetGravity(&gravity, &q);
      mpu.dmpGetLinearAccel(&aaReal, &aa, &gravity);
      mpu.dmpGetLinearAccelInWorld(&aaWorld, &aaReal, &q);
      Serial.print("Acceleration (x,y) m/s/s: ");
      Serial.print(aaWorld.x);
      Serial.print("  ");
      Serial.println(aaWorld.y);

     // Find the angle of acceleration
      //  double angle_of_acc = atan2(aaWorld.y, aaWorld.x);
      //  angle_of_acc *= 180/M_PI;

      // Get compass heading
      // mag.getHeading(&mx, &my, &mz);
      // float heading = atan2(my, mx);
      // if (heading < 0) heading += 2 * PI;
      // if (heading > 2 * PI) heading -= 2 * PI;
      // heading *= 180/M_PI;
      // heading += declination;

      // Offset angle of acceleration by the heading angle
      // wave_direction = angle_off_acc + heading
      
    }
}
```

### [Crude] Wave Energy

One way of defining wave energy is using this friendly equation:

Wave Power — [Source](https://en.wikipedia.org/wiki/Wave_power)*

Wave Power — [Source](https://en.wikipedia.org/wiki/Wave_power)*

Using our values for wave period and height, we are able to calculate wave energy like this:

```c++
// Wave power formula:  P = 0.5 height ** 2 * period // https://en.wikipedia.org/wiki/Wave_power 
#include "Wire.h"
#include "I2Cdev.h" //   Get these libraries from https://github.com/jrowberg/i2cdevlib/tree/master/Arduino
#include "MPU6050.h" //  ^
#include <MS5611.h> // Get this library from https://github.com/jarzebski/Arduino-MS5611

MPU6050 mpu;
MS5611 baro;

long pressure;
double altitude, min_height, max_height, wave_height, mid_point, smudge_factor, wave_power;
byte escaped, started;
unsigned long period_start, period_end;
float avg_period = -1;

void setup() {
  Serial.begin(115200);
  Wire.begin();
  Serial.println("Initializing I2C devices...");
  mpu.setI2CMasterModeEnabled(false);
  mpu.setI2CBypassEnabled(true) ;
  mpu.setSleepEnabled(false);
  mpu.initialize();
  Serial.println(mpu.testConnection() ? "MPU6050 connection successful" : "MPU6050 connection failed");
  while (!baro.begin(MS5611_ULTRA_HIGH_RES)) {
    Serial.println("MS5611 connection unsuccessful, check wiring!");
    delay(500);
  }
}

void loop() {
  unsigned long start_time = millis();
  pressure = baro.readPressure(true);
  altitude = baro.getAltitude(pressure);
  max_height = altitude;
  min_height = altitude;

  //  for 5 seconds
  while(millis() - start_time < 5000){
    pressure = baro.readPressure(true);
    altitude = baro.getAltitude(pressure);
    if (altitude < min_height) min_height = altitude;
    if (altitude > max_height) max_height = altitude;
  }
  mid_point = (max_height + min_height)/2.0;
  wave_height = (max_height - mid_point) / 2.0;
  smudge_factor = wave_height * 0.15;
  Serial.print("Wave Height m: "); Serial.print(wave_height);
  
  start_time = millis();
  //  for 5 seconds 
  while(millis() - start_time < 5000){
    pressure = baro.readPressure(true);
    altitude = baro.getAltitude(pressure);
    //    if within a range of 30% of wave height from the mid point
    //    start the timer else stop it
    if (altitude < mid_point + smudge_factor && altitude > mid_point - smudge_factor){
      if ( !started){
        period_start = millis();
        started = true;
      }
      else{
        if ( escaped ){
          // if it has started and escaped and is now returning
          period_end = millis();
          started = false;
          escaped = false;
          // if the variable has already been assigned
          // use its previous value and new value to work out avg
          if(avg_period != -1){
            avg_period = (avg_period + (period_end-period_start)*2)  / 2.0;
          }
          // assign it
          else{
            avg_period =  (period_end-period_start)*2; 
          }

        }
      }
    }
    else{
      escaped = true;
    } 
  }
  Serial.print("  Period s: "); Serial.print(avg_period/1000);
  wave_power = (0.5 * wave_height * wave_height * avg_period / 1000);
  Serial.print("  Wave Power kW/m: "); Serial.println(wave_power); 
}
```

### Water Temperature



Finally, we wanted to be able to measure water temperature. The DS18B20 water temperature sensor protrudes from the bottom of the Buoy into the sea and the Arduino communicates with it using 1-wire.

The only modification we made was adding a pull-up resistor on the signal wire, and then we were able to talk to it like this:

```c++
#include <onewire.h>
#include <dallastemperature.h>

OneWire oneWire(6);
DallasTemperature sensors(&oneWire);
float water_temperature;

void setup() {
  Serial.begin(115200);
  sensors.begin();
}

void loop() {
  sensors.requestTemperatures();
  water_temperature = sensors.getTempCByIndex(0);  
  Serial.print("Water temperature C "); Serial.println(water_temperature);
  delay(200);
}

```
> # [🔗 Get The Smart Buoy Code On Github 📔](https://github.com/sk-t3ch/smart-buoy)

## Thanks For Reading



Thanks for reading this tutorial, this has been the first step in building our Smart Buoy. Buckle up for the next tutorials!

[**Part 1**: Making wave and temperature measurements](https://t3chflicks.medium.com/smart-buoy-making-wave-and-temperature-measurements-%EF%B8%8F-cdda14c52196)

[**Part 2**: GPS, Radio (NRF24) and SD Card Module](https://t3chflicks.medium.com/smart-buoy-gps-radio-nrf24-and-a-sd-card-module-6029af3a69d)

[**Part 3**: Scheduling Power to the Buoy](https://t3chflicks.medium.com/smart-buoy-scheduling-power-to-the-system-81a2675fdac0)

[**Part 4**: Waterproofing, Dashboards and Deploy!](https://t3chflicks.medium.com/smart-buoy-waterproofing-dashboards-and-deploy-15c730bf9a3a)

We hope you enjoyed this article. If you like the style, check out [T3chFlicks.org](https://t3chflicks.org/) for more tech-focused educational content as well as all the fun stuff we do on [YouTube](https://www.youtube.com/channel/UC0eSD-tdiJMI5GQTkMmZ-6w) ([Instagram](https://www.instagram.com/t3chflicks/), [Facebook](https://www.facebook.com/t3chflicks), [Twitter](https://twitter.com/t3chflicks)).

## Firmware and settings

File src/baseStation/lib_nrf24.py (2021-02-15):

#!/usr/bin/python
# -*- coding: utf-8 -*-
#


# This file lib_nrf24.py is a slightly tweaked version of Barraca's "pynrf24".

# So this is my tweak for Raspberry Pi and "Virtual GPIO" ...
#       ... of Barraca's port to BeagleBone python ...  (Joao Paulo Barraca <jpbarraca@gmail.com>)
#                ... of maniacbug's NRF24L01 C++ library for Arduino.
# Brian Lavery Oct 2014



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


import sys
import time

if __name__ == '__main__':
    print (sys.argv[0], 'is an importable module:')
    print ("...  from", sys.argv[0], "import lib_nrf24")
    print ("")

    exit()

def _BV(x):
    return 1 << x


class NRF24:
    MAX_CHANNEL = 127
    MAX_PAYLOAD_SIZE = 32

    # PA Levels
    PA_MIN = 0
    PA_LOW = 1
    PA_HIGH = 2
    PA_MAX = 3
    PA_ERROR = 4

    # Bit rates
    BR_1MBPS = 0
    BR_2MBPS = 1
    BR_250KBPS = 2

    # CRC
    CRC_DISABLED = 0
    CRC_8 = 1
    CRC_16 = 2
    CRC_ENABLED = 3

    # Registers
    CONFIG = 0x00
    EN_AA = 0x01
    EN_RXADDR = 0x02
    SETUP_AW = 0x03
    SETUP_RETR = 0x04
    RF_CH = 0x05
    RF_SETUP = 0x06
    STATUS = 0x07
    OBSERVE_TX = 0x08
    CD = 0x09
    RX_ADDR_P0 = 0x0A
    RX_ADDR_P1 = 0x0B
    RX_ADDR_P2 = 0x0C
    RX_ADDR_P3 = 0x0D
    RX_ADDR_P4 = 0x0E
    RX_ADDR_P5 = 0x0F
    TX_ADDR = 0x10
    RX_PW_P0 = 0x11
    RX_PW_P1 = 0x12
    RX_PW_P2 = 0x13
    RX_PW_P3 = 0x14
    RX_PW_P4 = 0x15
    RX_PW_P5 = 0x16
    FIFO_STATUS = 0x17
    DYNPD = 0x1C
    FEATURE = 0x1D


    # Bit Mnemonics */
    MASK_RX_DR = 6
    MASK_TX_DS = 5
    MASK_MAX_RT = 4
    EN_CRC = 3
    CRCO = 2
    PWR_UP = 1
    PRIM_RX = 0
    ENAA_P5 = 5
    ENAA_P4 = 4
    ENAA_P3 = 3
    ENAA_P2 = 2
    ENAA_P1 = 1
    ENAA_P0 = 0
    ERX_P5 = 5
    ERX_P4 = 4
    ERX_P3 = 3
    ERX_P2 = 2
    ERX_P1 = 1
    ERX_P0 = 0
    AW = 0
    ARD = 4
    ARC = 0
    PLL_LOCK = 4
    RF_DR = 3
    RF_PWR = 6
    RX_DR = 6
    TX_DS = 5
    MAX_RT = 4
    RX_P_NO = 1
    TX_FULL = 0
    PLOS_CNT = 4
    ARC_CNT = 0
    TX_REUSE = 6
    FIFO_FULL = 5
    TX_EMPTY = 4
    RX_FULL = 1
    RX_EMPTY = 0
    DPL_P5 = 5
    DPL_P4 = 4
    DPL_P3 = 3
    DPL_P2 = 2
    DPL_P1 = 1
    DPL_P0 = 0
    EN_DPL = 2
    EN_ACK_PAY = 1
    EN_DYN_ACK = 0

    # Instruction Mnemonics
    R_REGISTER = 0x00
    W_REGISTER = 0x20
    REGISTER_MASK = 0x1F
    ACTIVATE = 0x50
    R_RX_PL_WID = 0x60
    R_RX_PAYLOAD = 0x61
    W_TX_PAYLOAD = 0xA0
    W_ACK_PAYLOAD = 0xA8
    FLUSH_TX = 0xE1
    FLUSH_RX = 0xE2
    REUSE_TX_PL = 0xE3
    NOP = 0xFF


    # Non-P omissions
    LNA_HCURR = 0x00

    # P model memory Map
    RPD = 0x09

    # P model bit Mnemonics
    RF_DR_LOW = 5
    RF_DR_HIGH = 3
    RF_PWR_LOW = 1
    RF_PWR_HIGH = 2

    # Signal Mnemonics
    LOW = 0
    HIGH = 1

    datarate_e_str_P = ["1MBPS", "2MBPS", "250KBPS"]
    model_e_str_P = ["nRF24L01", "nRF24l01+"]
    crclength_e_str_P = ["Disabled", "8 bits", "16 bits"]
    pa_dbm_e_str_P = ["PA_MIN", "PA_LOW", "PA_MED", "PA_HIGH"]
    child_pipe = [RX_ADDR_P0, RX_ADDR_P1, RX_ADDR_P2, RX_ADDR_P3, RX_ADDR_P4, RX_ADDR_P5]

    child_payload_size = [RX_PW_P0, RX_PW_P1, RX_PW_P2, RX_PW_P3, RX_PW_P4, RX_PW_P5]
    child_pipe_enable = [ERX_P0, ERX_P1, ERX_P2, ERX_P3, ERX_P4, ERX_P5]

    GPIO = None
    spidev = None

    def __init__(self, gpio, spidev):
        # It should be possible to instantiate multiple objects, with different GPIO / spidev
        # EG on Raspberry, one could be RPI GPIO & spidev module, other could be virtual-GPIO
        # On rpi, only bus 0 is supported here, not bus 1 of the model B plus
        self.GPIO = gpio   # the GPIO module
        self.spidev = spidev # the spidev object/instance
        self.channel = 76
        self.data_rate = NRF24.BR_1MBPS
        self.wide_band = False # 2Mbs data rate in use?
        self.p_variant = False # False for RF24L01 and true for RF24L01P (nrf24l01+)
        self.payload_size = 5 #*< Fixed size of payloads
        self.ack_payload_available = False #*< Whether there is an ack payload waiting
        self.dynamic_payloads_enabled = False #*< Whether dynamic payloads are enabled.
        self.ack_payload_length = 5 #*< Dynamic size of pending ack payload.
        self.pipe0_reading_address = None #*< Last address set on pipe 0 for reading.

    def ce(self, level):
        if self.ce_pin == 0:
            return
        # rf24-CE is optional. Tie to HIGH if not used. (Altho, left floating seems to read HIGH anyway??? - risky!)
        # Some RF24 modes may NEED control over CE.
        # non-powerdown, fixed PTX or RTX role, dynamic payload size & ack-payload:    does NOT need CE.
        if level == NRF24.HIGH:
            self.GPIO.output(self.ce_pin, self.GPIO.HIGH)
        else:
            self.GPIO.output(self.ce_pin, self.GPIO.LOW)
        return



    def read_register(self, reg, blen=1):
        buf = [NRF24.R_REGISTER | ( NRF24.REGISTER_MASK & reg )]
        for col in range(blen):
            buf.append(NRF24.NOP)

        resp = self.spidev.xfer2(buf)
        if blen == 1:
            return resp[1]

        return resp[1:blen + 1]

    def write_register(self, reg, value, length=-1):
        buf = [NRF24.W_REGISTER | ( NRF24.REGISTER_MASK & reg )]
        ###if isinstance(value, (int, long)):   # ng for python3. but value should never be long anyway
        if isinstance(value, int):
            if length < 0:
                length = 1

            length = min(4, length)
            for i in range(length):
                buf.insert(1, int(value & 0xff))
                value >>= 8

        elif isinstance(value, list):
            if length < 0:
                length = len(value)

            for i in range(min(len(value), length)):
                buf.append(int(value[len(value) - i - 1] & 0xff))
        else:
            raise Exception("Value must be int or list")

        return self.spidev.xfer2(buf)[0]


    def write_payload(self, buf):
        data_len = min(self.payload_size, len(buf))
        blank_len = 0
        if not self.dynamic_payloads_enabled:
            blank_len = self.payload_size - data_len

        txbuffer = [NRF24.W_TX_PAYLOAD]
        for n in buf:
            t = type(n)
            if t is str:
                txbuffer.append(ord(n))
            elif t is int:
                txbuffer.append(n)
            else:
                raise Exception("Only ints and chars are supported: Found " + str(t))

        if blank_len != 0:
            blank = [0x00 for i in range(blank_len)]
            txbuffer.extend(blank)

        return self.spidev.xfer2(txbuffer)

    def read_payload(self, buf, buf_len=-1):
        if buf_len < 0:
            buf_len = self.payload_size
        data_len = min(self.payload_size, buf_len)
        blank_len = 0
        if not self.dynamic_payloads_enabled:
            blank_len = self.payload_size - data_len

        txbuffer = [NRF24.NOP for i in range(0, blank_len + data_len + 1)]
        txbuffer[0] = NRF24.R_RX_PAYLOAD

        payload = self.spidev.xfer2(txbuffer)
        del buf[:]
        buf.extend(payload[1:data_len + 1])
        return data_len

    def flush_rx(self):
        return self.spidev.xfer2([NRF24.FLUSH_RX])[0]

    def flush_tx(self):
        return self.spidev.xfer2([NRF24.FLUSH_TX])[0]

    def get_status(self):
        return self.spidev.xfer2([NRF24.NOP])[0]

    def print_status(self, status):
        status_str = "STATUS\t = 0x{0:02x} RX_DR={1:x} TX_DS={2:x} MAX_RT={3:x} RX_P_NO={4:x} TX_FULL={5:x}".format(
            status,
            1 if status & _BV(NRF24.RX_DR) else 0,
            1 if status & _BV(NRF24.TX_DS) else 0,
            1 if status & _BV(NRF24.MAX_RT) else 0,
            ((status >> NRF24.RX_P_NO) & 7),
            1 if status & _BV(NRF24.TX_FULL) else 0)

        print (status_str)

    def print_observe_tx(self, value):
        print ("Observe Tx: %02x   Lost Pkts: %d    Retries: %d" % (value, value >> NRF24.PLOS_CNT, value & 15))


    def print_byte_register(self, name, reg, qty=1):
        extra_tab = '\t' if len(name) < 8 else 0
        print ("%s\t%c =" % (name, extra_tab)),
        while qty > 0:
            print ("0x%02x" % (self.read_register(reg))),
            qty -= 1
            reg += 1

        print ("")

    def print_address_register(self, name, reg, qty=1):
        extra_tab = '\t' if len(name) < 8 else 0
        print ("%s\t%c =" % (name, extra_tab)),

        while qty > 0:
            qty -= 1
            buf = reversed(self.read_register(reg, 5))
            reg += 1
            sys.stdout.write(" 0x"),
            for i in buf:
                sys.stdout.write("%02x" % i)

        print ("")


    def setChannel(self, channel):
        self.channel = min(max(0, channel), NRF24.MAX_CHANNEL)
        self.write_register(NRF24.RF_CH, self.channel)

    def getChannel(self):
        return self.read_register(NRF24.RF_CH)

    def setPayloadSize(self, size):
        self.payload_size = min(max(size, 1), NRF24.MAX_PAYLOAD_SIZE)

    def getPayloadSize(self):
        return self.payload_size

    def printDetails(self):
        self.print_status(self.get_status())
        self.print_address_register("RX_ADDR_P0-1", NRF24.RX_ADDR_P0, 2)
        self.print_byte_register("RX_ADDR_P2-5", NRF24.RX_ADDR_P2, 4)
        self.print_address_register("TX_ADDR", NRF24.TX_ADDR)

        self.print_byte_register("RX_PW_P0-6", NRF24.RX_PW_P0, 6)
        self.print_byte_register("EN_AA", NRF24.EN_AA)
        self.print_byte_register("EN_RXADDR", NRF24.EN_RXADDR)
        self.print_byte_register("RF_CH", NRF24.RF_CH)
        self.print_byte_register("RF_SETUP", NRF24.RF_SETUP)
        self.print_byte_register("CONFIG", NRF24.CONFIG)
        self.print_byte_register("DYNPD/FEATURE", NRF24.DYNPD, 2)

        #
        print ("Data Rate\t = %s" % NRF24.datarate_e_str_P[self.getDataRate()])
        print ("Model\t\t = %s" % NRF24.model_e_str_P[self.isPVariant()])
        print ("CRC Length\t = %s" % NRF24.crclength_e_str_P[self.getCRCLength()])
        print ("PA Power\t = %s" % NRF24.pa_dbm_e_str_P[self.getPALevel()])

    def begin(self, csn_pin, ce_pin=0):   # csn & ce are RF24 terminology. csn = SPI's CE!
        # Initialize SPI bus..
        # ce_pin is for the rx=listen or tx=trigger pin on RF24 (they call that ce !!!)
        # CE optional (at least in some circumstances, eg fixed PTX PRX roles, no powerdown)
        # CE seems to hold itself as (sufficiently) HIGH, but tie HIGH is safer!
        self.spidev.open(0, csn_pin)
        self.spidev.max_speed_hz = 1000000
        self.ce_pin = ce_pin

        if ce_pin:
            self.GPIO.setup(self.ce_pin, self.GPIO.OUT)

        time.sleep(5 / 1000000.0)

        # Set 1500uS (minimum for 32B payload in ESB@250KBPS) timeouts, to make testing a little easier
        # WARNING: If this is ever lowered, either 250KBS mode with AA is broken or maximum packet
        # sizes must never be used. See documentation for a more complete explanation.
        self.write_register(NRF24.SETUP_RETR, (0b0100 << NRF24.ARD) | 0b1111)

        # Restore our default PA level
        self.setPALevel(NRF24.PA_MAX)

        # Determine if this is a p or non-p RF24 module and then
        # reset our data rate back to default value. This works
        # because a non-P variant won't allow the data rate to
        # be set to 250Kbps.
        if self.setDataRate(NRF24.BR_250KBPS):
            self.p_variant = True

        # Then set the data rate to the slowest (and most reliable) speed supported by all
        # hardware.
        self.setDataRate(NRF24.BR_1MBPS)

        # Initialize CRC and request 2-byte (16bit) CRC
        self.setCRCLength(NRF24.CRC_16)

        # Disable dynamic payloads, to match dynamic_payloads_enabled setting
        self.write_register(NRF24.DYNPD, 0)

        # Reset current status
        # Notice reset and flush is the last thing we do
        self.write_register(NRF24.STATUS, _BV(NRF24.RX_DR) | _BV(NRF24.TX_DS) | _BV(NRF24.MAX_RT))

        # Set up default configuration.  Callers can always change it later.
        # This channel should be universally safe and not bleed over into adjacent
        # spectrum.
        self.setChannel(self.channel)

        # Flush buffers
        self.flush_rx()
        self.flush_tx()

    def end(self):
        if self.spidev:
            self.spidev.close()
            self.spidev = None

    def startListening(self):
        self.write_register(NRF24.CONFIG, self.read_register(NRF24.CONFIG) | _BV(NRF24.PWR_UP) | _BV(NRF24.PRIM_RX))
        self.write_register(NRF24.STATUS, _BV(NRF24.RX_DR) | _BV(NRF24.TX_DS) | _BV(NRF24.MAX_RT))

        # Restore the pipe0 address, if exists
        if self.pipe0_reading_address:
            self.write_register(self.RX_ADDR_P0, self.pipe0_reading_address, 5)

        # Go!
        self.ce(NRF24.HIGH)

        # wait for the radio to come up (130us actually only needed)
        time.sleep(130 / 1000000.0)

    def stopListening(self):
        self.ce(NRF24.LOW)
        self.flush_tx()
        self.flush_rx()

    def powerDown(self):
        self.write_register(NRF24.CONFIG, self.read_register(NRF24.CONFIG) & ~_BV(NRF24.PWR_UP))

    def powerUp(self):
        self.write_register(NRF24.CONFIG, self.read_register(NRF24.CONFIG) | _BV(NRF24.PWR_UP))
        time.sleep(150 / 1000000.0)

    def write(self, buf):
        # Begin the write
        self.startWrite(buf)

        timeout = self.getMaxTimeout() #s to wait for timeout
        sent_at = time.time()

        while True:
            #status = self.read_register(NRF24.OBSERVE_TX, 1)
            status = self.get_status()
            if (status & (_BV(NRF24.TX_DS) | _BV(NRF24.MAX_RT))) or (time.time() - sent_at > timeout ):
                break
            time.sleep(10 / 1000000.0)
        #obs = self.read_register(NRF24.OBSERVE_TX)
        #self.print_observe_tx(obs)
        #self.print_status(status)
        # (for debugging)

        what = self.whatHappened()

        result = what['tx_ok']
        if what['tx_fail']:
            self.flush_tx();    # bl  - dont jam up the fifo
        # Handle the ack packet
        if what['rx_ready']:
            self.ack_payload_length = self.getDynamicPayloadSize()
            self.ack_payload_available = True              ## bl

        return result

    def startWrite(self, buf):
        # Transmitter power-up
        self.write_register(NRF24.CONFIG, (self.read_register(NRF24.CONFIG) | _BV(NRF24.PWR_UP) ) & ~_BV(NRF24.PRIM_RX))

        # Send the payload
        self.write_payload(buf)

        # Allons!
        if self.ce_pin:
            if self.GPIO.RPI_REVISION > 0:
                self.ce(self.GPIO.HIGH)
                time.sleep(10 / 1000000.0)
                self.ce(self.GPIO.LOW)
            else:
                # virtGPIO is slower. A 10 uSec pulse is better done with pulseOut():
                self.GPIO.pulseOut(self.ce_pin, self.GPIO.HIGH, 10)



    def getDynamicPayloadSize(self):
        return self.spidev.xfer2([NRF24.R_RX_PL_WID, NRF24.NOP])[1]

    def available(self, pipe_num=None):
        if not pipe_num:
            pipe_num = []

        status = self.get_status()
        result = False

        # Sometimes the radio specifies that there is data in one pipe but
        # doesn't set the RX flag...
        if status & _BV(NRF24.RX_DR) or (status & 0b00001110 != 0b00001110):
            result = True

        if result:
            # If the caller wants the pipe number, include that
            if len(pipe_num) >= 1:
                pipe_num[0] = ( status >> NRF24.RX_P_NO ) & 0b00000111

                # Clear the status bit

                # ??? Should this REALLY be cleared now?  Or wait until we
                # actually READ the payload?
        self.write_register(NRF24.STATUS, _BV(NRF24.RX_DR))

        # Handle ack payload receipt
        if status & _BV(NRF24.TX_DS):
            self.write_register(NRF24.STATUS, _BV(NRF24.TX_DS))

        return result

    def read(self, buf, buf_len=-1):
        # Fetch the payload
        self.read_payload(buf, buf_len)

        # was this the last of the data available?
        return self.read_register(NRF24.FIFO_STATUS) & _BV(NRF24.RX_EMPTY)

    def whatHappened(self):
        # Read the status & reset the status in one easy call
        # Or is that such a good idea?
        status = self.write_register(NRF24.STATUS, _BV(NRF24.RX_DR) | _BV(NRF24.TX_DS) | _BV(NRF24.MAX_RT))

        # Report to the user what happened
        tx_ok = status & _BV(NRF24.TX_DS)
        tx_fail = status & _BV(NRF24.MAX_RT)
        rx_ready = status & _BV(NRF24.RX_DR)
        return {'tx_ok': tx_ok, "tx_fail": tx_fail, "rx_ready": rx_ready}

    def openWritingPipe(self, value):
        # Note that the NRF24L01(+)
        # expects it LSB first.

        self.write_register(NRF24.RX_ADDR_P0, value, 5)
        self.write_register(NRF24.TX_ADDR, value, 5)

        max_payload_size = 32
        self.write_register(NRF24.RX_PW_P0, min(self.payload_size, max_payload_size))

    def openReadingPipe(self, child, address):
        # If this is pipe 0, cache the address.  This is needed because
        # openWritingPipe() will overwrite the pipe 0 address, so
        # startListening() will have to restore it.
        if child == 0:
            self.pipe0_reading_address = address

        if child <= 6:
            # For pipes 2-5, only write the LSB
            if child < 2:
                self.write_register(NRF24.child_pipe[child], address, 5)
            else:
                self.write_register(NRF24.child_pipe[child], address, 1)

            self.write_register(NRF24.child_payload_size[child], self.payload_size)

            # Note it would be more efficient to set all of the bits for all open
            # pipes at once.  However, I thought it would make the calling code
            # more simple to do it this way.
            self.write_register(NRF24.EN_RXADDR,
                                self.read_register(NRF24.EN_RXADDR) | _BV(NRF24.child_pipe_enable[child]))


    def closeReadingPipe(self, pipe):
        self.write_register(NRF24.EN_RXADDR,
            self.read_register(EN_RXADDR) & ~_BV(NRF24.child_pipe_enable[pipe]))


    def toggle_features(self):
        buf = [NRF24.ACTIVATE, 0x73]
        self.spidev.xfer2(buf)

    def enableDynamicPayloads(self):
        # Enable dynamic payload throughout the system
        self.write_register(NRF24.FEATURE, self.read_register(NRF24.FEATURE) | _BV(NRF24.EN_DPL))

        # If it didn't work, the features are not enabled
        if not self.read_register(NRF24.FEATURE):
            # So enable them and try again
            self.toggle_features()
            self.write_register(NRF24.FEATURE, self.read_register(NRF24.FEATURE) | _BV(NRF24.EN_DPL))

        # Enable dynamic payload on all pipes

        # Not sure the use case of only having dynamic payload on certain
        # pipes, so the library does not support it.
        self.write_register(NRF24.DYNPD, self.read_register(NRF24.DYNPD) | _BV(NRF24.DPL_P5) | _BV(NRF24.DPL_P4) | _BV(
            NRF24.DPL_P3) | _BV(NRF24.DPL_P2) | _BV(NRF24.DPL_P1) | _BV(NRF24.DPL_P0))

        self.dynamic_payloads_enabled = True


    def enableAckPayload(self):
        # enable ack payload and dynamic payload features
        self.write_register(NRF24.FEATURE,
                            self.read_register(NRF24.FEATURE) | _BV(NRF24.EN_ACK_PAY) | _BV(NRF24.EN_DPL))

        # If it didn't work, the features are not enabled
        if not self.read_register(NRF24.FEATURE):
            # So enable them and try again
            self.toggle_features()
            self.write_register(NRF24.FEATURE,
                                self.read_register(NRF24.FEATURE) | _BV(NRF24.EN_ACK_PAY) | _BV(NRF24.EN_DPL))

        # Enable dynamic payload on pipes 0 & 1
        self.write_register(NRF24.DYNPD, self.read_register(NRF24.DYNPD) | _BV(NRF24.DPL_P1) | _BV(NRF24.DPL_P0))

    def writeAckPayload(self, pipe, buf, buf_len):
        txbuffer = [NRF24.W_ACK_PAYLOAD | ( pipe & 0x7 )]

        max_payload_size = 32
        data_len = min(buf_len, max_payload_size)
        txbuffer.extend(buf[0:data_len])

        self.spidev.xfer2(txbuffer)

    def isAckPayloadAvailable(self):
        result = self.ack_payload_available
        self.ack_payload_available = False
        return result

    def isPVariant(self):
        return self.p_variant

    def setAutoAck(self, enable):
        if enable:
            self.write_register(NRF24.EN_AA, 0b111111)
        else:
            self.write_register(NRF24.EN_AA, 0)

    def setAutoAckPipe(self, pipe, enable):
        if pipe <= 6:
            en_aa = self.read_register(NRF24.EN_AA)
            if enable:
                en_aa |= _BV(pipe)
            else:
                en_aa &= ~_BV(pipe)

            self.write_register(NRF24.EN_AA, en_aa)

    def testCarrier(self):
        return self.read_register(NRF24.CD) & 1

    def testRPD(self):
        return self.read_register(NRF24.RPD) & 1

    def setPALevel(self, level):
        setup = self.read_register(NRF24.RF_SETUP)
        setup &= ~( _BV(NRF24.RF_PWR_LOW) | _BV(NRF24.RF_PWR_HIGH))
        # switch uses RAM (evil!)
        if level == NRF24.PA_MAX:
            setup |= (_BV(NRF24.RF_PWR_LOW) | _BV(NRF24.RF_PWR_HIGH))
        elif level == NRF24.PA_HIGH:
            setup |= _BV(NRF24.RF_PWR_HIGH)
        elif level == NRF24.PA_LOW:
            setup |= _BV(NRF24.RF_PWR_LOW)
        elif level == NRF24.PA_MIN:
            nop = 0
        elif level == NRF24.PA_ERROR:
            # On error, go to maximum PA
            setup |= (_BV(NRF24.RF_PWR_LOW) | _BV(NRF24.RF_PWR_HIGH))

        self.write_register(NRF24.RF_SETUP, setup)


    def getPALevel(self):
        power = self.read_register(NRF24.RF_SETUP) & (_BV(NRF24.RF_PWR_LOW) | _BV(NRF24.RF_PWR_HIGH))
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

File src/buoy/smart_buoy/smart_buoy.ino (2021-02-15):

/*
 * T3chFlicks - Smart Buoy Project
 * Find full tutorial including video, schematic, and links 
 * to components at https://t3chflicks.com/shop/kit/smart-buoy/
*/

#include <Wire.h>


struct measurement{
  byte index; // 1 byte
  unsigned long date; // 4 bytes
  unsigned long time; // 4 bytes
  float val_1; // 4 bytes
  float val_2; // 4 bytes
  float val_3; // 4 bytes
  float val_4; // 4 bytes 
  int val_5; // 2 bytes .... 31 bytes in total
}measurement_1, measurement_2;

// measurement_1 = {
// i =1
// date
// time
// latitude
// longitude
// current
// voltage
// wait time
// }

// measurement_2 = {
// i =2
// date
// time
// wave height
// wave period
// water temp
// air temp
// wave power
// }

#define TCAADDR 0x70

void tcaselect(uint8_t i) {
  if (i > 7) return;
 
  Wire.beginTransmission(TCAADDR);
  Wire.write(1 << i);
  Wire.endTransmission();  
}

void setup() {
  setup_gps();
  setup_radio();
  setup_gy86();
  setup_power_control();
  setup_water_temperature();
  measurement_1.index = 1;
  measurement_2.index = 2;
}

void loop() {
  get_gps_data();
  get_wave_stats();
  get_water_temperature();
  set_new_alarm();
  send_data();
  delay(3000); // seemed to help radio communication reliability
  turn_off();
}

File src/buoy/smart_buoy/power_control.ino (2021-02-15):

#include <DS3232RTC.h>
#include <Adafruit_INA219.h>

Adafruit_INA219 ina219;

void setup_power_control(){
  Wire.begin();
  ina219.begin();
  ina219.setCalibration_32V_1A();
}

void set_new_alarm(){
  int wait_time = get_wait_time_from_voltage();
  measurement_1.val_5 = wait_time;
  
  tcaselect(4);
  RTC.alarmInterrupt(ALARM_1, true);
  RTC.squareWave(SQWAVE_NONE);
  setTime(0, 0, 0, 1, 1, 1970);
  RTC.set(now());
  
  // set new alarm
  RTC.setAlarm(ALM1_MATCH_MINUTES, 0, wait_time, 0, 1);
}

int get_wait_time_from_voltage(){
  float shuntvoltage = ina219.getShuntVoltage_mV();
  float busvoltage = ina219.getBusVoltage_V();
  float loadvoltage = busvoltage + (shuntvoltage / 1000);
  measurement_1.val_3 = ina219.getCurrent_mA();
  measurement_1.val_4 = loadvoltage;

  // Samsung 18650 % capacity at a given voltage
  // batt_voltages            0.0, 3.4, 3.5, 3.6, 3.7, 3.8, 3.9, 4.0, 4.1, 4.2, 4.5
  // batt_percentages           0,   0,   9,  22,  52,  64,  75,  84,  93, 100, 100
  int wait_time;
  if (loadvoltage < 3.6) wait_time = 15;
  else if (loadvoltage < 3.8) wait_time = 10;
  else if (loadvoltage < 4.0) wait_time = 6;
  else if (loadvoltage < 4.1) wait_time = 3;
  else wait_time = 2;
  
  return wait_time;
}

void turn_off(){
  // clear old alarm flag - turning off system
  RTC.alarm(ALARM_1);
}

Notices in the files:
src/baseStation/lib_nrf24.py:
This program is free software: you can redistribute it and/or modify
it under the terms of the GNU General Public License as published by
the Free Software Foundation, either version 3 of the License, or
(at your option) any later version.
